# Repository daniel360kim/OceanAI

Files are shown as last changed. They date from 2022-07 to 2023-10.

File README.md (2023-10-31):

<!-- Project Logo -->
<div align="center">

<a href="https://github.com/daniel360kim/OceanAI">
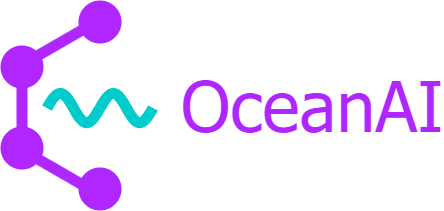
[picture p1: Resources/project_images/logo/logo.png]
    
</a>
  <h1 align="center">OceanAI</h1>
  
  <p align="center">
    A robotic and software orientated ocean development.
    <br />
    <a href="https://www.youtube.com/watch?v=8TJVxcPY-2g&t=32s&ab_channel=NMRocketry"><strong>See the video »</strong></a>
    <br />
    <br />
  </p>
</div>

<br>
  <h2>Table of Contents</h2>
  <ol>
    <li>
      <a href="#about-the-project">About The Project</a>
    </li>
    <li>
      <a href="#getting-started">Getting Started</a>
      <ul>
        <li><a href="#AUV Software">AUV Software</a></li>
        <li><a href="#Graphical User Interface">Graphical User Interface</a></li>
      </ul>
    </li>
    <li><a href="#license">License</a></li>
    <li><a href="#contact">Contact</a></li>
  </ol>

# About the Project
This project aims at creating an autonomous underwater vehicle (AUV) that utilizes cameras, sensors, a microcontroller, and GPS to categorize, identify, and map underwater trash. Detection of litter will be performed with a deep learning model - optimized to run on a microcontroller - allowing for cheap and power-efficient inference of underwater footage.

Main components of the project include:
* [AUV Control Board](https://github.com/daniel360kim/OceanAI/tree/master/PCBs)
* [AUV Software](https://github.com/daniel360kim/OceanAI/tree/master/software/sub_driver)
* [AUV CAD Model](https://github.com/daniel360kim/OceanAI/tree/master/CAD)
* [Deep Learning Model](https://github.com/daniel360kim/OceanAI/tree/master/software/detection_model)

# Getting Started
## AUV Software
[VSCode](https://code.visualstudio.com/) and
[PlatformIO](https://platformio.org/) are used to build and upload the software to the AUV.
1. Install VSCode and the PlatformIO extension.
2. Clone the repository.
```sh
git clone https://github.com/daniel360kim/OceanAI.git
```
3. Go to PlatformIO home and go to the 'Projects' tab.
4. Click 'Add Existing Project' and select the `software/sub_driver` folder.
5. Make sure you have the Teensy 4.1 core installed.
6. Connect the AUV through USB and click the 'Upload' button.
<br></br>

## Graphical User Interface

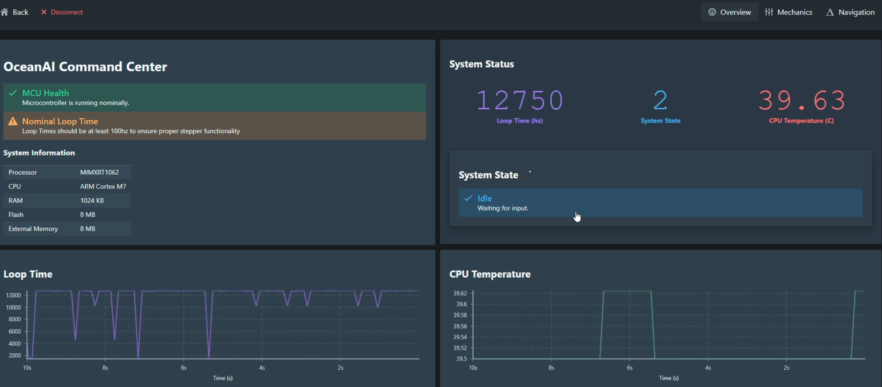
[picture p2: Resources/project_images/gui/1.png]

<br></br>
The GUI is built using [ElectricUI](https://electricui.com/). ElectricUI requires:
* [Node.js](https://nodejs.org/en/)
* [Yarn](https://yarnpkg.com/)

1. Install Node.js, [available from their website](https://nodejs.org/en/).
2. Install Yarn.
```sh
npm install -g yarn
```
3. Install ElectricUI, [available here](https://registry.eui.io/arc/latest/arc_latest_windows_amd64.msi)
4. Check everything installed and can be found in your PATH
```sh
arc info
```
5. Clone the repository if you haven't already.
```sh
git clone https://github.com/daniel360kim/OceanAI.git
```
6. Open the GUI project with ElectricUI. `software/auv_gui`
7. Run the GUI.
```sh
arc start
```

# License
Distributed under the MIT License. See `LICENSE` for more information.

# Contact
* Daniel Kim - nmrs.thrust@gmail.com - [YouTube](https://www.youtube.com/channel/UC0VazqJrUQiJGd_Tedn47zA) - Instagram: @us_rockets
* Project Link: https://github.com/daniel360kim/OceanAI

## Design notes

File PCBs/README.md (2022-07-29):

# PCBs
## Contains all the files for the printed circuit boards.
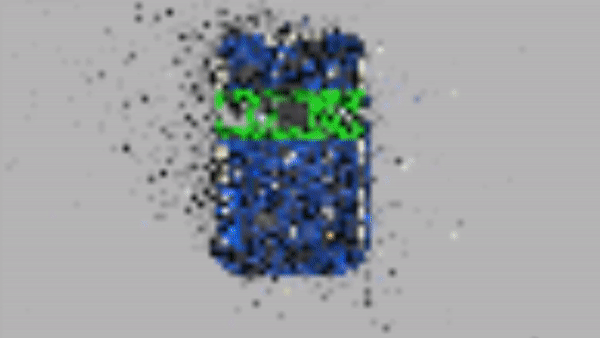
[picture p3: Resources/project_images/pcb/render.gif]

### main_board
* The PCB on the submarine that controls the submarine.
* This is the main board that controls navigation, outputs, loggins etc.

### transmitter_board
* This is an optional module that is floating in the water.
* It is connnected through a cable to the main board.
* It is above water so it can access GPS, RF, and other radio frequencies.

### sensor_board
* This board is at the front of the submarine. 
* It reads the underwater sensors and sends the data to the main board through I2C.
* It is not self powered - must have a clean 3.3V power supply.
* Programmed through SWD.

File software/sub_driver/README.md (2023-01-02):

# Sub Driver Software

Software to control the submarine driver board.

## Build
The project's directories are built with PlatformIO. To build the project, open the project in PlatformIO and click the build button.

## Dependencies Modifications
Dependencies can be modified by going to the .pio/libdeps directory within the project. 

* Must delete 
    ```cpp
    #define swap 
    ```

From Arducam dependencies to resolve conflicts with the standard library.
* Must delete utility folder from Buzzer library and remove the include from the source header file.
* Remove:
```cpp
# include "utility/pitches.h"
```
From Buzzer.h

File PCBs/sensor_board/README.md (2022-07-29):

# Transmitter Board
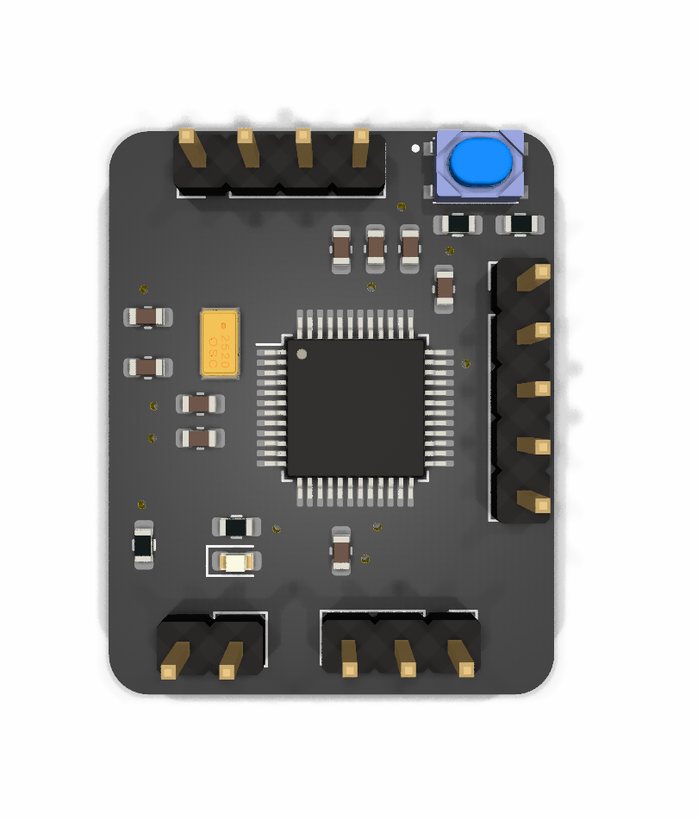
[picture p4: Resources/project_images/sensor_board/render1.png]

## This directory contains the PCB designs for the sensor board.
### The front of the submarine contains several sensors underwater: a pressure transducer and a thermistor. The pressure transducer is used to measure the pressure of the water. The thermistor is used to measure the temperature of the water. The sensor board reads these sensors and sends the data to the main board through I2C. 
### Power:
* 3.3V (no voltage regulator onboard - must be clean 3.3V)
### Sensors:
* Analog input for external pressure transducer
* 10K Thermistor for water temperature readings
### Communication:
* Communicated to the submarine [main_board](https://github.com/daniel360kim/OceanAI/tree/master/main_board) through I2C.
* The board features SWD interface for debugging and is programmed through SWD.

## What's done?
* Schematic is finished.
* PCB layout is finished
* 3D models and fabrication outputs are generated
## What's to do?
* Ordering and fabrication

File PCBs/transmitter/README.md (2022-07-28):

# Transmitter Board
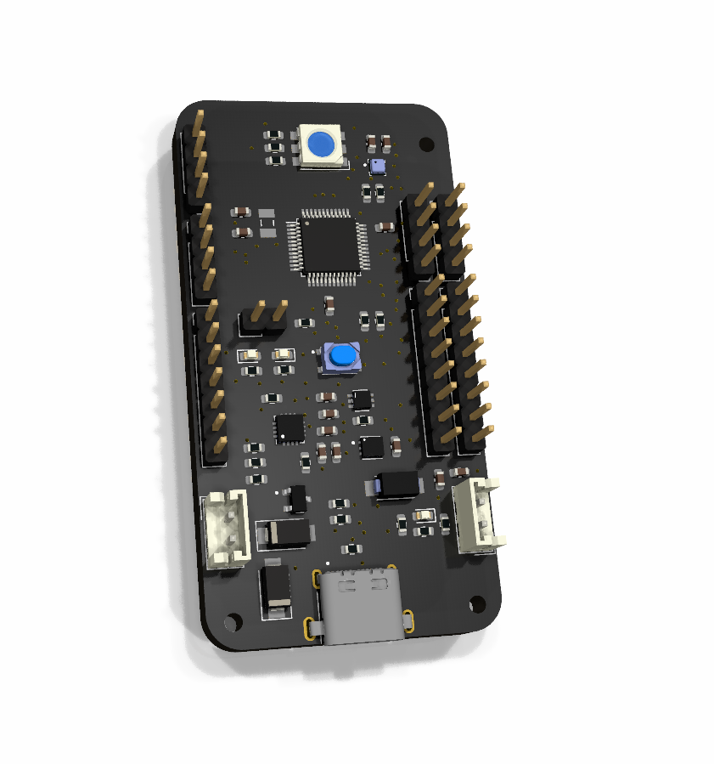
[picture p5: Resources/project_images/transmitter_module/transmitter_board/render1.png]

## This directory contains the PCB designs for the transmitter board.
### Since RF and GPS do not function well underwater, the submarine will feature an optional transmitter module that is floating in the water. The transmitter board is a simple, inexpensive, and easy to use module that can be used to transmit data to the submarine. Powered by the ATSAMD21G18A, the board has several features:
### Power:
* 1S LiPo battery 
* Solar power to recharge LiPo battery
### Sensors:
* BMP388 pressure sensor
* 10K Thermistor for water temperature readings
### Communication:
* Communicated to the submarine [main_board](https://github.com/daniel360kim/OceanAI/tree/master/main_board) through an ethernet cable through I2C.
* I2C optimized for long range communication using the LTC4311 chip.
* The board has 2 SPI interfaces: One for a 2.4GHz RF module and one for a LoRa radio module.
* The board has a UART interface for GPS connectivity.
* The board features SWD interface for debugging. 

## What's done?
* Schematic is finished.
* PCB layout is finished
* 3D models and fabrication outputs are generated
## What's to do?
* Ordering and fabrication

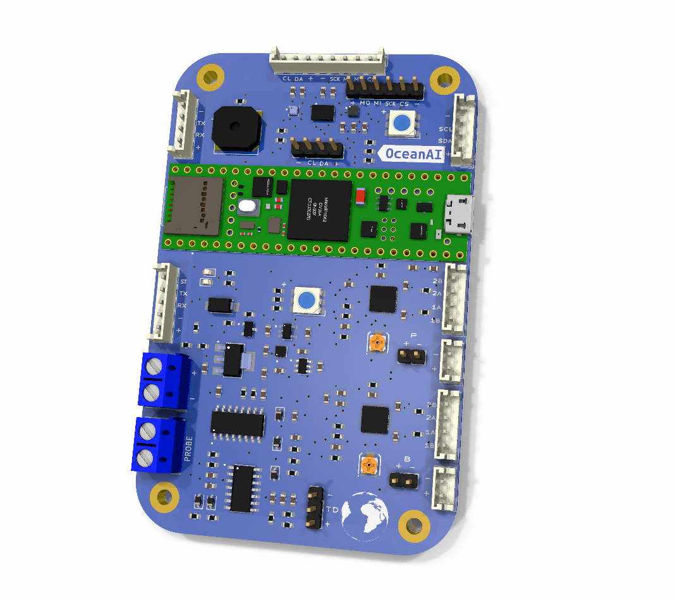
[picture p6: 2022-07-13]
PCBs/main_board/main_board_png/front_render.png

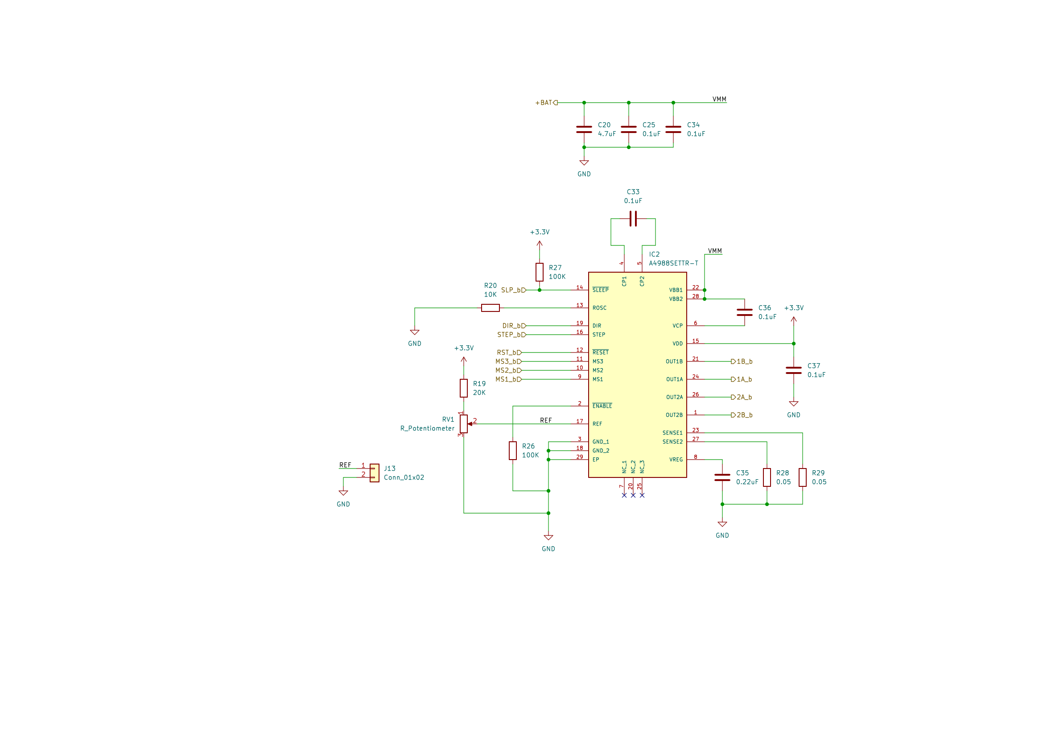
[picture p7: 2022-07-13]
PCBs/main_board/main_board_png/sch_rev2-05.png

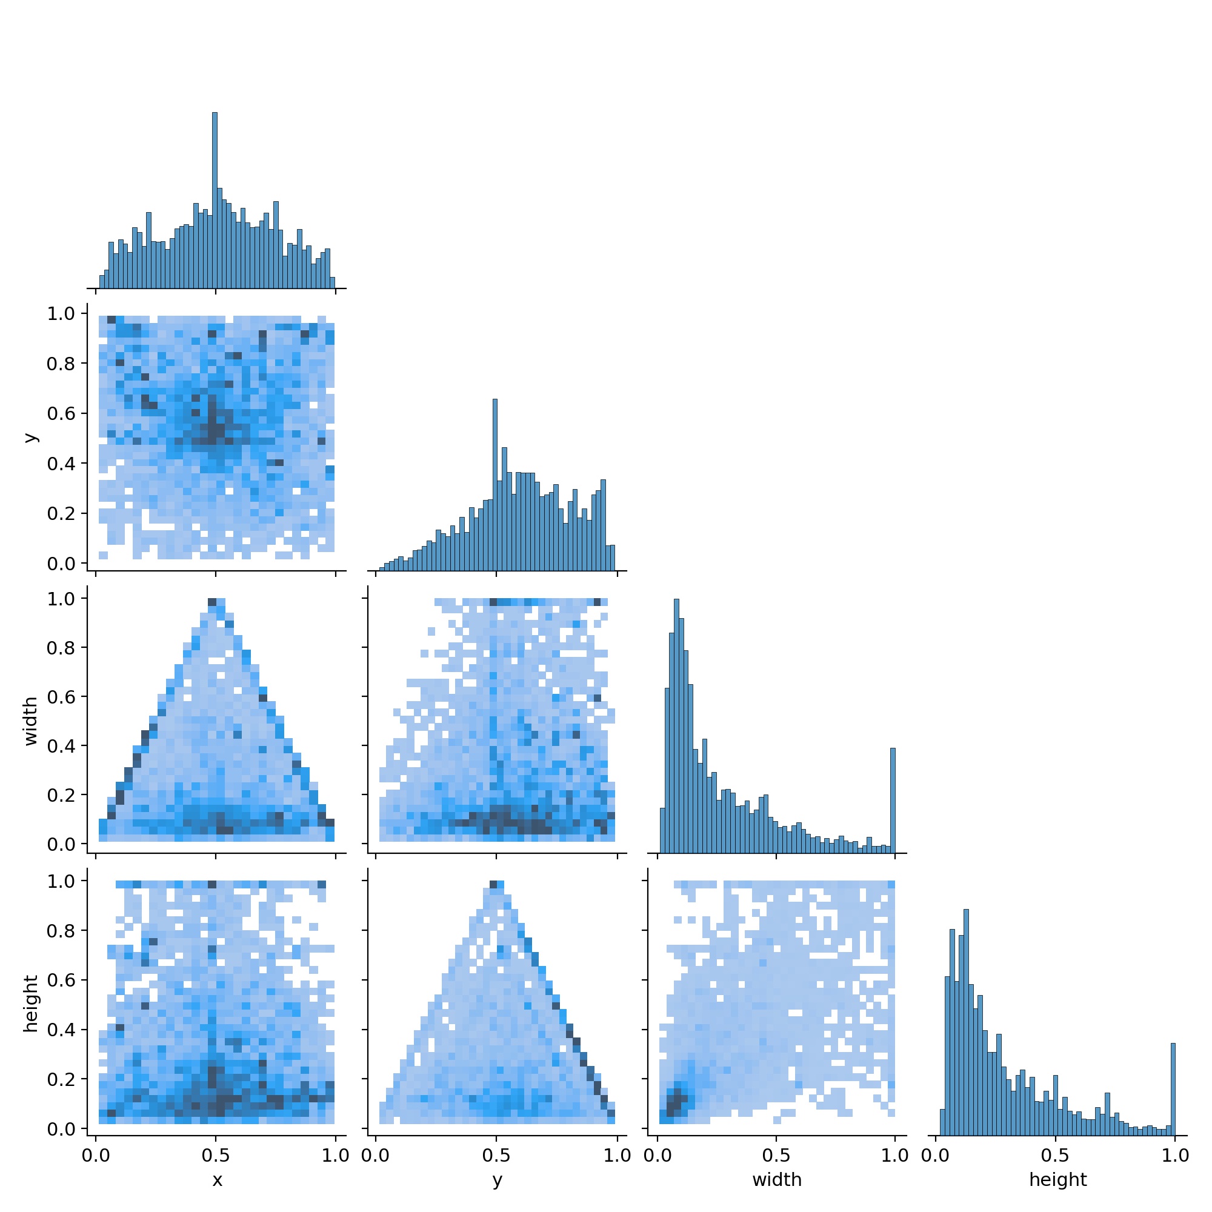
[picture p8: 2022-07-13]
Resources/project_images/object_detection/Run 1/04994b5c-de77-487a-9553-cd7c2c360d0d.jpg

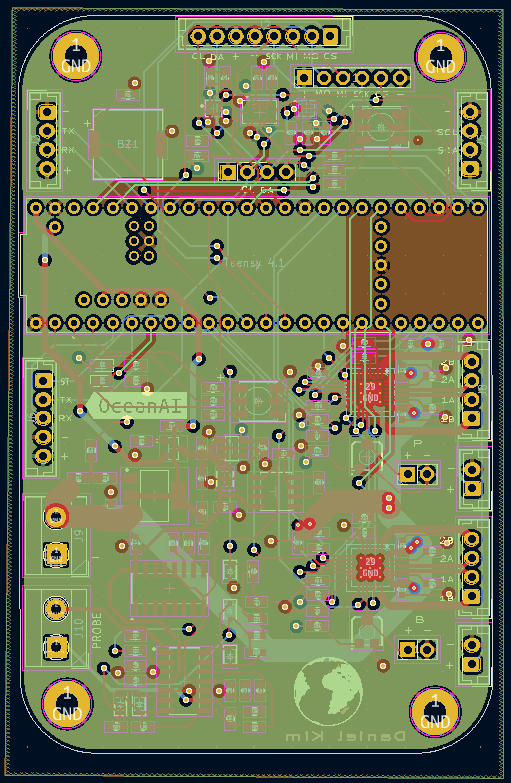
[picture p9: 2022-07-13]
PCBs/main_board/main_board_png/inner1.png

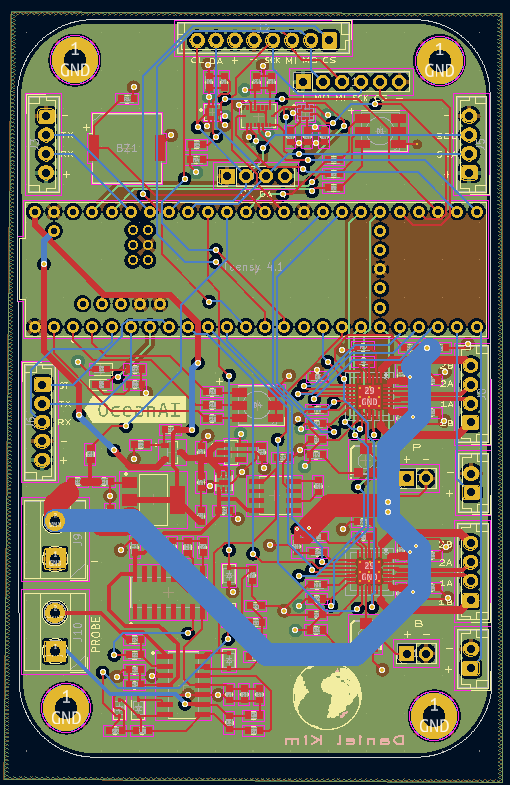
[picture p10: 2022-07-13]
PCBs/main_board/main_board_png/bottom.png

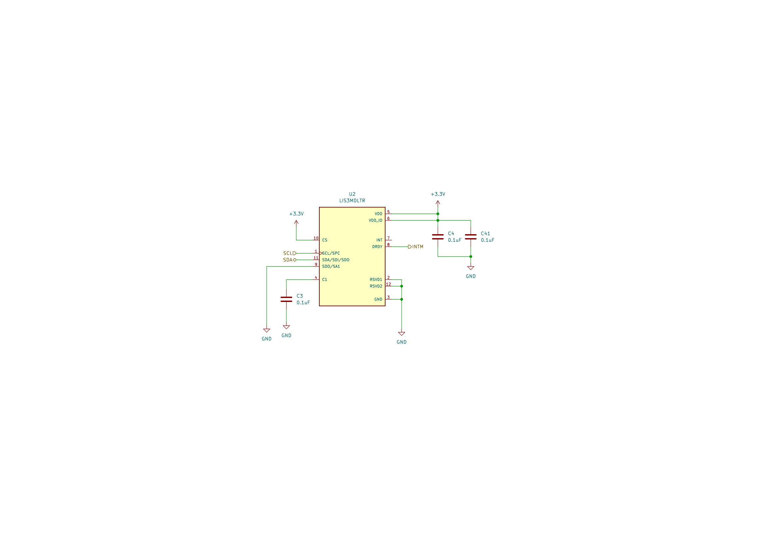
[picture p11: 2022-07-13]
PCBs/main_board/main_board_png/sch_rev2-03.png

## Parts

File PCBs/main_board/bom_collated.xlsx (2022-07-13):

Item | Item | Item | Value | LibPart | Footprint
1 | 1 | BZ1 | Buzzer | Device:Buzzer | Buzzer_Beeper:Buzzer_Murata_PKMCS0909E
2 | 21 | C1, C2, C3, C4, C5, C6, C8, C9, C14, C15, C25, C27, C28, C29, C31, C32, C33, C34, C36, C37, C41 | 0.1uF | Device:C | Capacitor_SMD:C_0603_1608Metric
3 | 1 | C7 | 1nF | Device:C | Capacitor_SMD:C_0603_1608Metric
4 | 7 | C10, C13, C17, C19, C21, C22, C24 | 1uF | Device:C | Capacitor_SMD:C_0603_1608Metric
5 | 5 | C11, C12, C20, C23, C26 | 4.7uF | Device:C | Capacitor_SMD:C_0603_1608Metric
6 | 2 | C16, C18 | 10uF | Device:C | Capacitor_SMD:C_0603_1608Metric
7 | 2 | C30, C35 | 0.22uF | Device:C | Capacitor_SMD:C_0603_1608Metric
8 | 5 | D1, D2, D3, D4, D5 | 1N4148WS | Diode:1N4148WS | Diode_SMD:D_SOD-323
9 | 2 | D6, D7 | LED_RGB | Device:LED_RGB | LED_SMD:LED_RGB_5050-6
10 | 2 | D8, D9 | LED | Device:LED | LED_SMD:LED_0603_1608Metric
11 | 4 | H1, H2, H3, H4 | MountingHole_Pad | Mechanical:MountingHole_Pad | MountingHole:MountingHole_3mm_Pad
12 | 2 | IC1, IC2 | A4988SETTR-T | A4988SETTR-T:A4988SETTR-T | A4988SETTR-T:QFN50P500X500X100-29N
13 | 1 | J1 | MS5803 | Connector_Generic:Conn_01x04 | Connector_JST:JST_EH_B4B-EH-A_1x04_P2.50mm_Vertical
14 | 1 | J2 | I2C | Connector_Generic:Conn_01x04 | Connector_PinHeader_2.54mm:PinHeader_1x04_P2.54mm_Vertical
15 | 1 | J3 | PROBE | Connector_Generic:Conn_01x02 | TerminalBlock_MetzConnect:TerminalBlock_MetzConnect_Type101_RT01602HBWC_1x02_P5.08mm_Horizontal
16 | 1 | J4 | Batt | Connector_Generic:Conn_01x02 | TerminalBlock_MetzConnect:TerminalBlock_MetzConnect_Type101_RT01602HBWC_1x02_P5.08mm_Horizontal
17 | 1 | J5 | OV5642 | Connector_Generic:Conn_01x08 | Connector_JST:JST_EH_B8B-EH-A_1x08_P2.50mm_Vertical
18 | 1 | J6 | JST_B | Connector_Generic:Conn_01x04 | Connector_JST:JST_EH_B4B-EH-A_1x04_P2.50mm_Vertical
19 | 1 | J7 | JST_P | Connector_Generic:Conn_01x04 | Connector_JST:JST_EH_B4B-EH-A_1x04_P2.50mm_Vertical
20 | 1 | J8 | I2C | Connector_Generic:Conn_01x06 | Connector_PinHeader_2.54mm:PinHeader_1x06_P2.54mm_Vertical
21 | 1 | J9 | HC-12 | Connector_Generic:Conn_01x05 | Connector_JST:JST_EH_B5B-EH-A_1x05_P2.50mm_Vertical
22 | 1 | J10 | NEO-6M | Connector_Generic:Conn_01x04 | Connector_JST:JST_EH_B4B-EH-A_1x04_P2.50mm_Vertical
23 | 1 | J11 | Limit_b | Connector_Generic:Conn_01x02 | Connector_JST:JST_EH_B2B-EH-A_1x02_P2.50mm_Vertical
24 | 1 | J12 | Limit_p | Connector_Generic:Conn_01x02 | Connector_JST:JST_EH_B2B-EH-A_1x02_P2.50mm_Vertical
25 | 2 | J13, J14 | Conn_01x02 | Connector_Generic:Conn_01x02 | Connector_PinHeader_2.54mm:PinHeader_1x02_P2.54mm_Vertical
26 | 1 | Q1 | DMP3098L-7 | DMP3098L-7:DMP3098L-7 | DMP3098L-7:SOT91P240X110-3N
27 | 1 | R1 | 1M | Device:R | Resistor_SMD:R_0603_1608Metric
28 | 3 | R2, R3, R39 | 4.7K | Device:R | Resistor_SMD:R_0603_1608Metric
29 | 1 | R4 | 5.6K | Device:R | Resistor_SMD:R_0603_1608Metric
30 | 1 | R5 | 6.8K | Device:R | Resistor_SMD:R_0603_1608Metric
31 | 6 | R6, R8, R22, R23, R26, R27 | 100K | Device:R | Resistor_SMD:R_0603_1608Metric
32 | 10 | R7, R9, R10, R11, R12, R13, R14, R15, R20, R21 | 10K | Device:R | Resistor_SMD:R_0603_1608Metric
33 | 1 | R16 | 2.5 | Device:R | Resistor_SMD:R_0603_1608Metric
34 | 4 | R17, R18, R31, R41 | 1K | Device:R | Resistor_SMD:R_0603_1608Metric
35 | 2 | R19, R30 | 20K | Device:R | Resistor_SMD:R_0603_1608Metric
36 | 4 | R24, R25, R28, R29 | 0.05 | Device:R | Resistor_SMD:R_0603_1608Metric
37 | 4 | R33, R35, R36, R38 | R | Device:R | Resistor_SMD:R_0603_1608Metric
38 | 2 | R34, R37 |  | Device:R | Resistor_SMD:R_0603_1608Metric
39 | 1 | R40 | 470 | Device:R | Resistor_SMD:R_0603_1608Metric
40 | 2 | RV1, RV2 | R_Potentiometer | Device:R_Potentiometer | 35WR10KLFTR:TRIM_35WR10KLFTR
41 | 1 | U1 | BMI088 | TBC_Sensors:BMI088 | BMI088:PQFN50P450X300X100-16N
42 | 1 | U2 | LIS3MDLTR | LIS3MDLTR:LIS3MDLTR | LIS3MDLTR:XDCR_LIS3MDLTR
43 | 1 | U3 | BMP388 | TBC_Sensors:BMP388 | BMP388:PQFN50P200X200X80-10N
44 | 1 | U4 | DEV-16771 | DEV-16771:DEV-16771 | DEV-16771:MODULE_DEV-16771
45 | 1 | U5 | LM324A | :LM324A_1 | LM324:SOIC127P600X175-14N
46 | 1 | U6 | CD4060BM | CD4060BM:CD4060BM | CD4060BM:SOIC127P600X175-16N
47 | 1 | U7 | ICL7662CBA-T | ICL7662CBA-T:ICL7662CBA-T | ICL7662CBA-T:SOIC127P600X175-8N
48 | 1 | U8 | AP2112K-3.3 | Regulator_Linear:AP2112K-3.3 | AP2112K-3:SOT95P285X140-5N
49 | 1 | U9 | ADP122 | ADP122:ADP122ACPZ-3.3-R7 | ADP122:SON65P200X200X65-7N
50 | 1 | U10 | LDL1117S50R | Regulator_Linear:LDL1117S50R | SOT230P700X180-4N:SOT230P700X180-4N

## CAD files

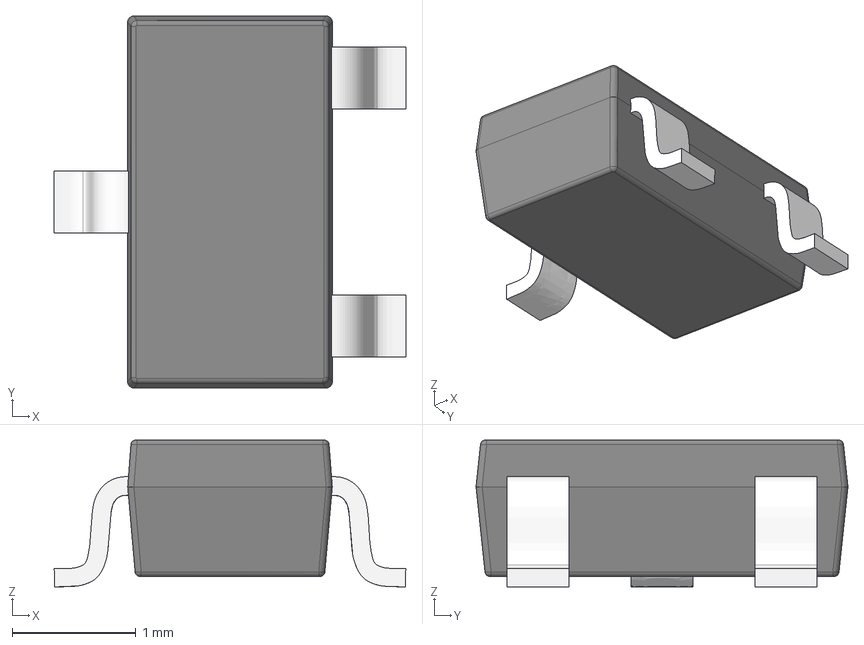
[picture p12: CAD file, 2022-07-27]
PCBs/transmitter/Dependencies/SOT23-3.stp
2.84 x 3.00 x 1.18 mm

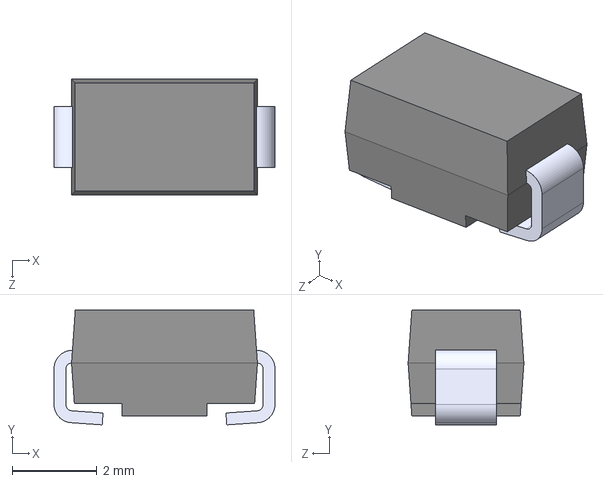
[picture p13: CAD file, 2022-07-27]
PCBs/transmitter/Dependencies/SS12.STEP
5.20 x 2.70 x 2.73 mm

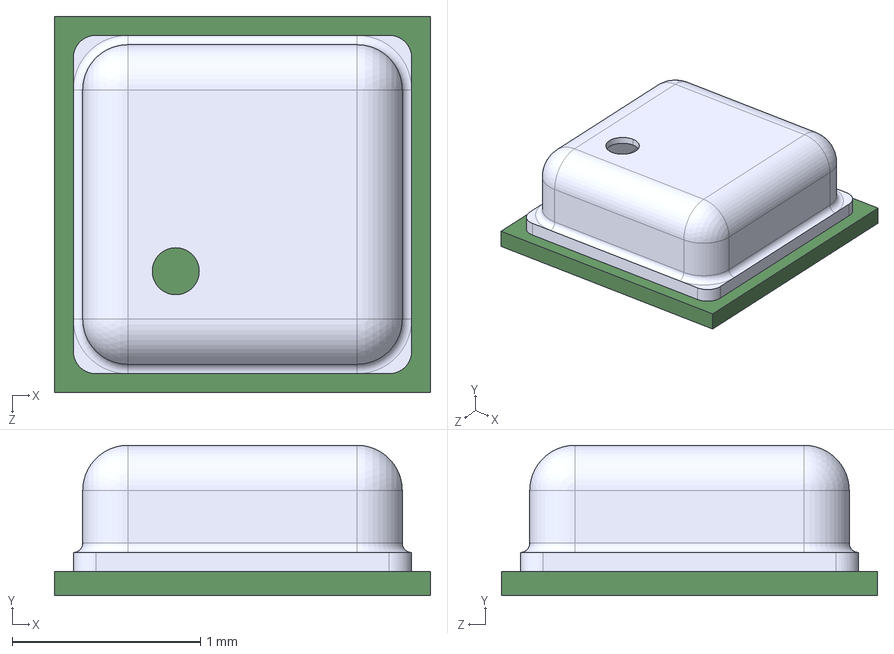
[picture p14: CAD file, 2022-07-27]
PCBs/transmitter/Dependencies/BMP388.STEP
2.00 x 0.8 x 2.00 mm

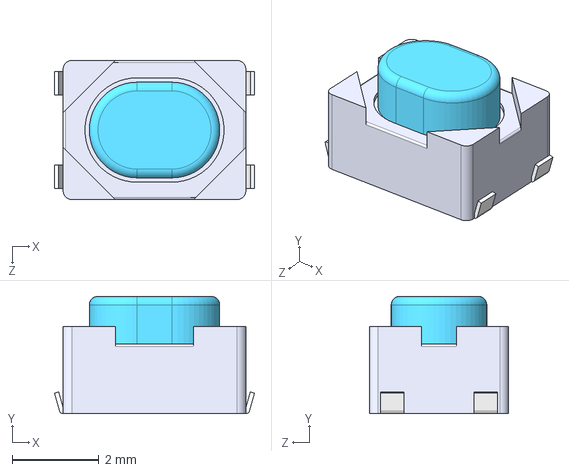
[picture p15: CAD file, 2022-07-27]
PCBs/transmitter/Dependencies/PTS810SJK250SMTRLFS.step
4.60 x 2.70 x 3.20 mm

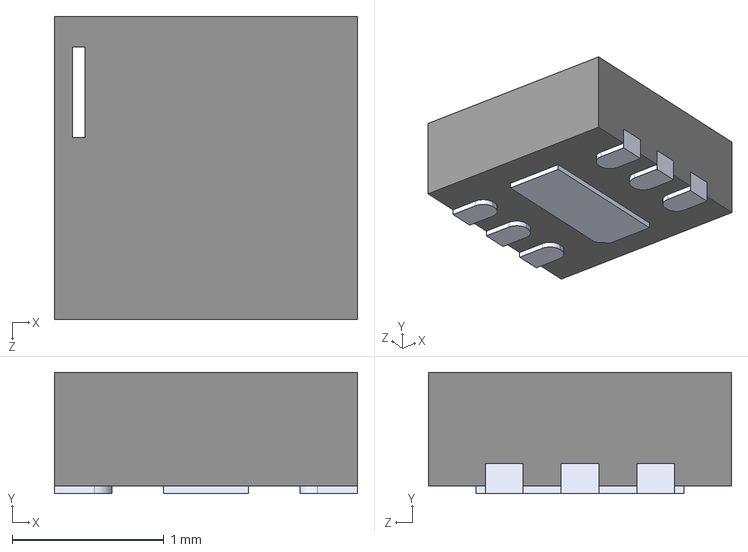
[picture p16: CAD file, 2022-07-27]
PCBs/transmitter/Dependencies/LTC4311IDCPBF.step
2.00 x 0.8 x 2.00 mm

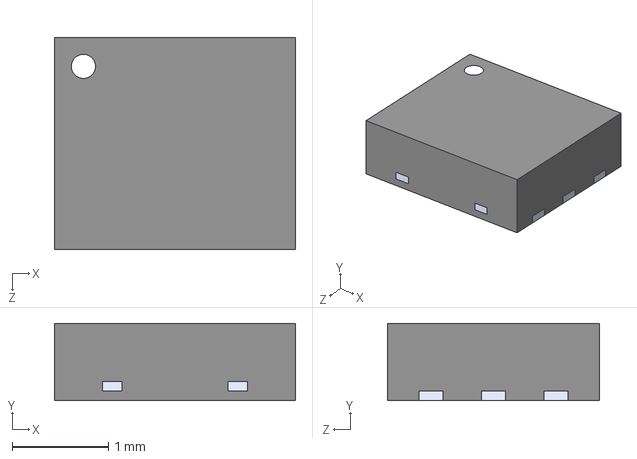
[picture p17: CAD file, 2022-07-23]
PCBs/transmitter/Dependencies/LP5900SD-3.3_NOPB.step
2.50 x 0.8 x 2.20 mm

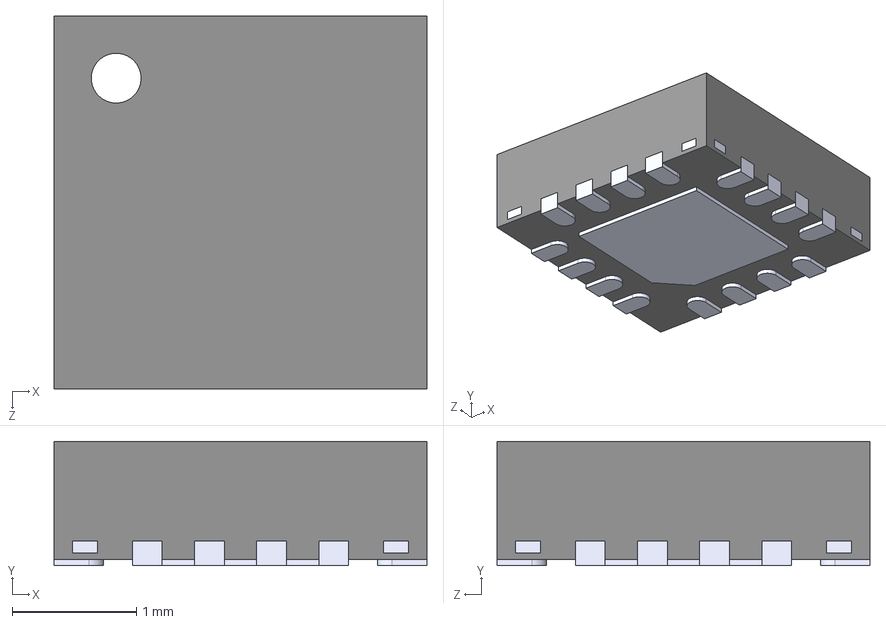
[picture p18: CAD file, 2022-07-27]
PCBs/transmitter/Dependencies/BQ24074RGTRG4.STEP
3.00 x 1.00 x 3.00 mm

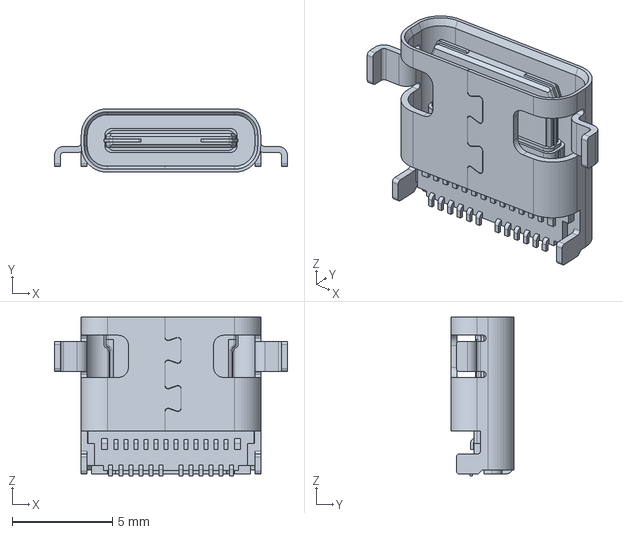
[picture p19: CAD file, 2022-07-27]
PCBs/transmitter/Dependencies/1054550101.step
11.6 x 3.16 x 7.90 mm

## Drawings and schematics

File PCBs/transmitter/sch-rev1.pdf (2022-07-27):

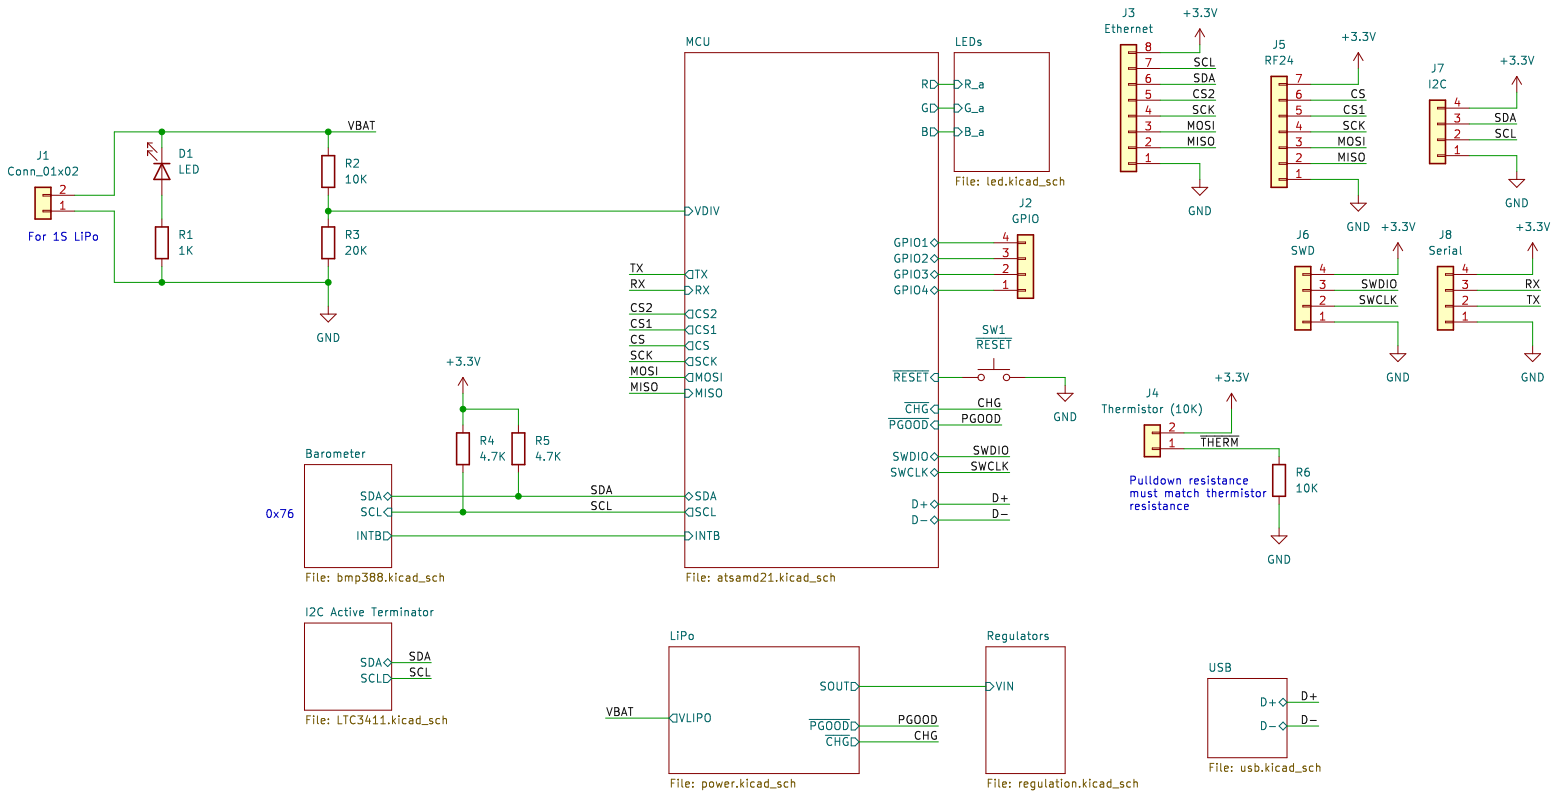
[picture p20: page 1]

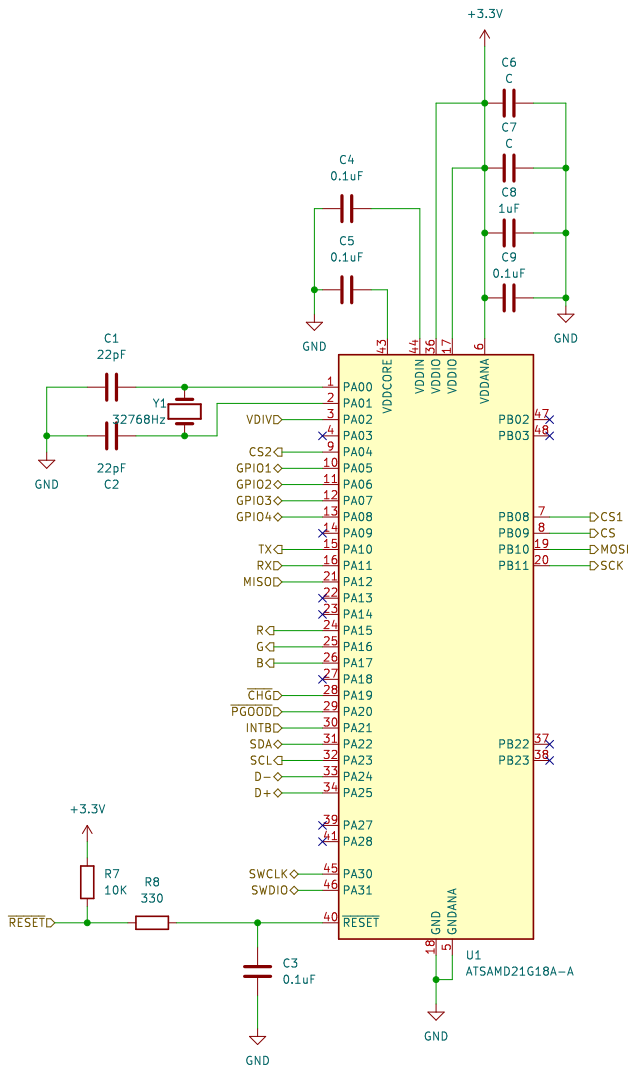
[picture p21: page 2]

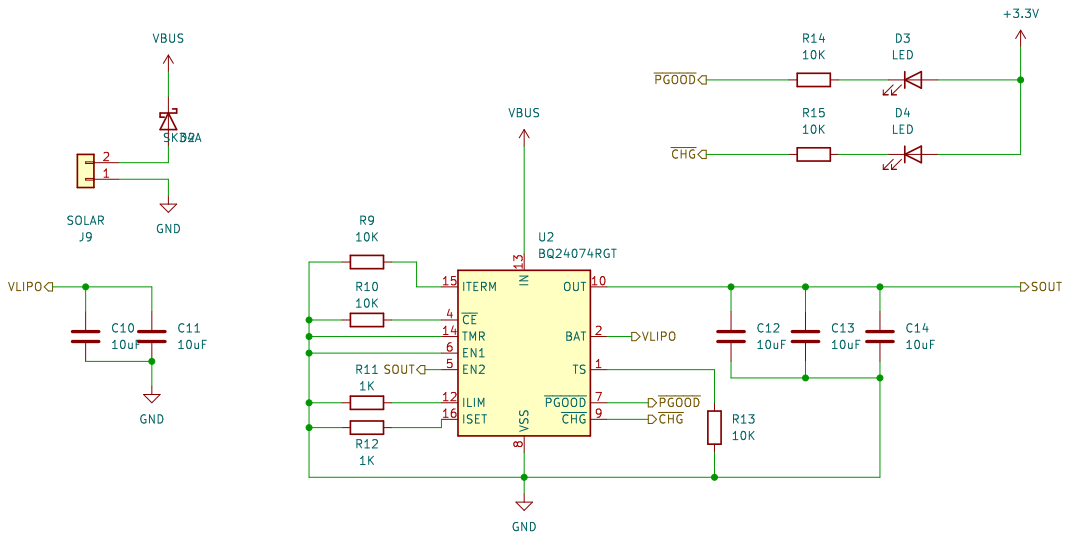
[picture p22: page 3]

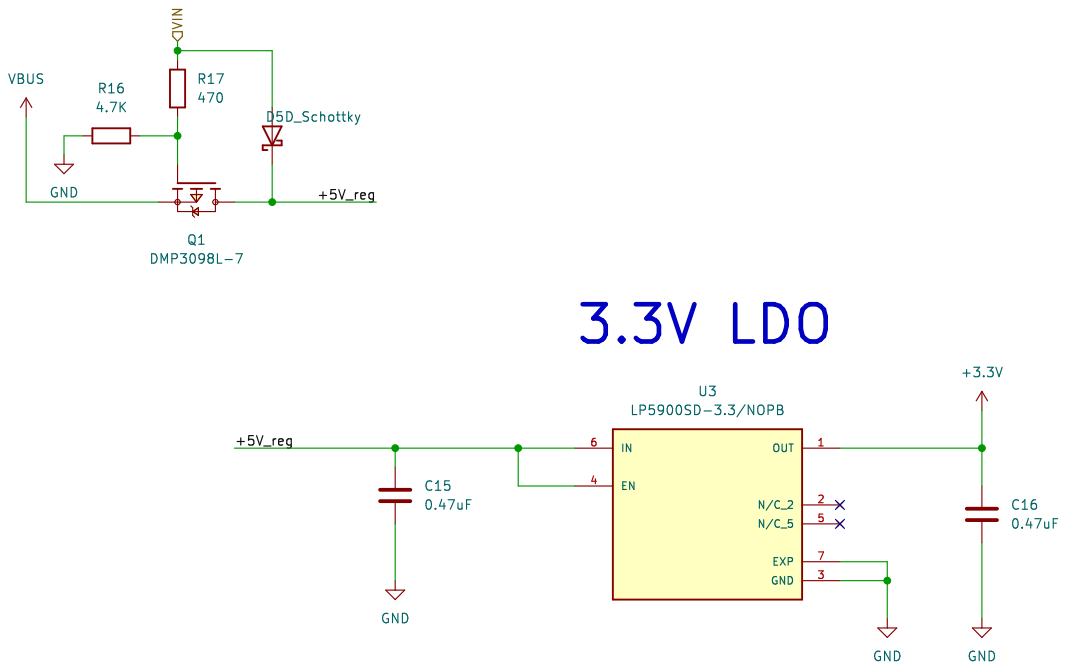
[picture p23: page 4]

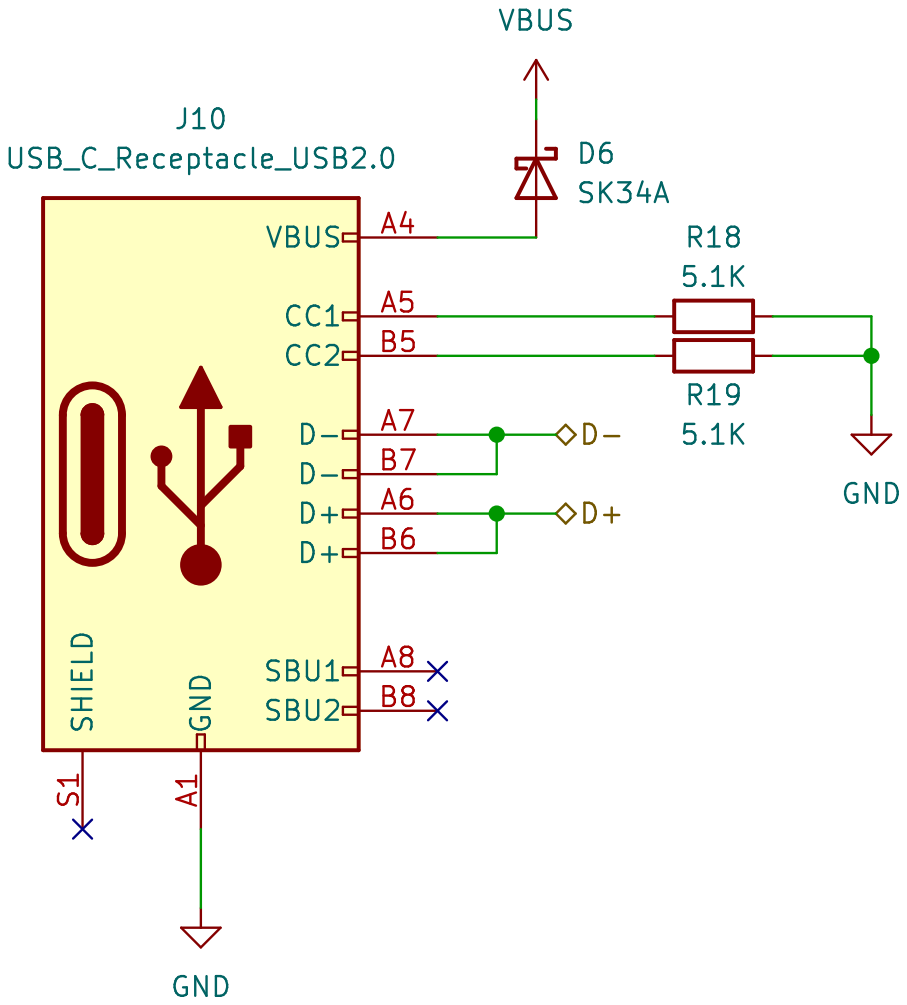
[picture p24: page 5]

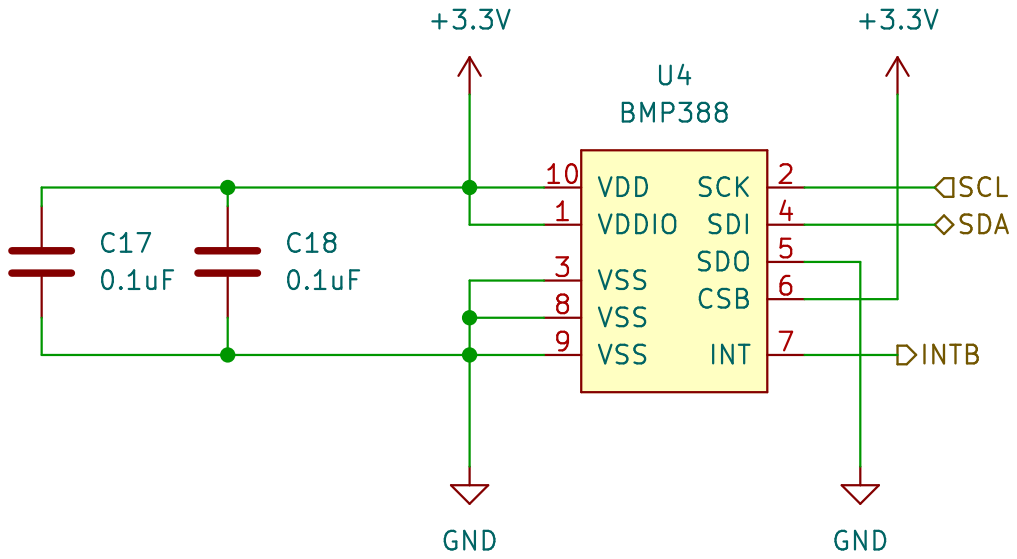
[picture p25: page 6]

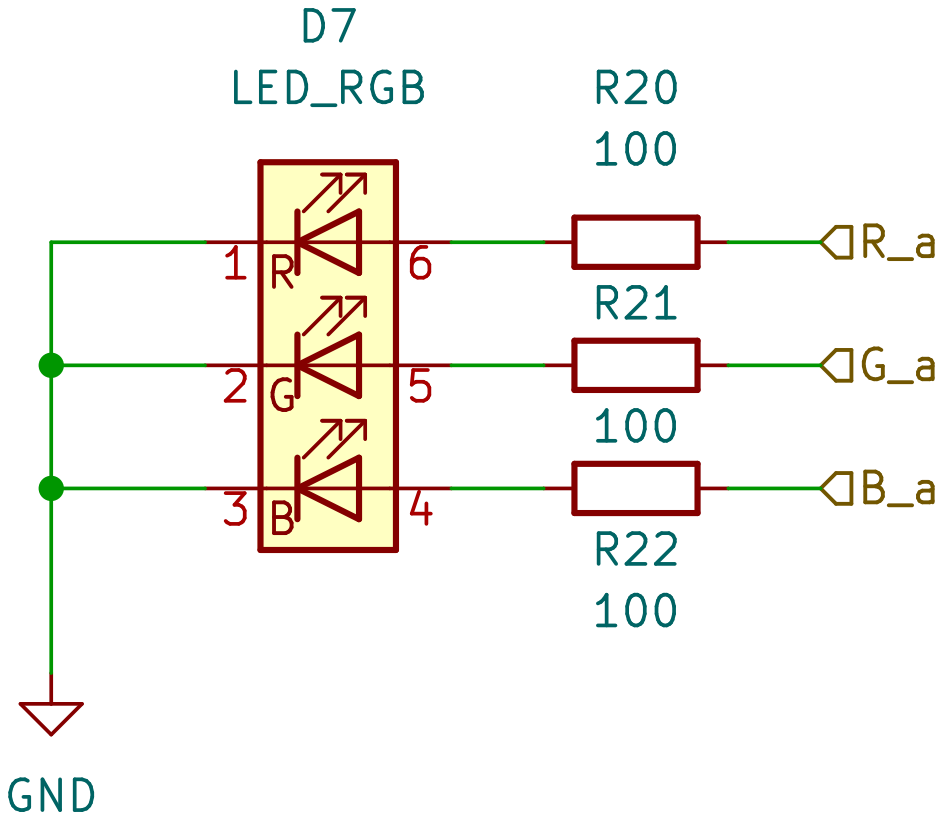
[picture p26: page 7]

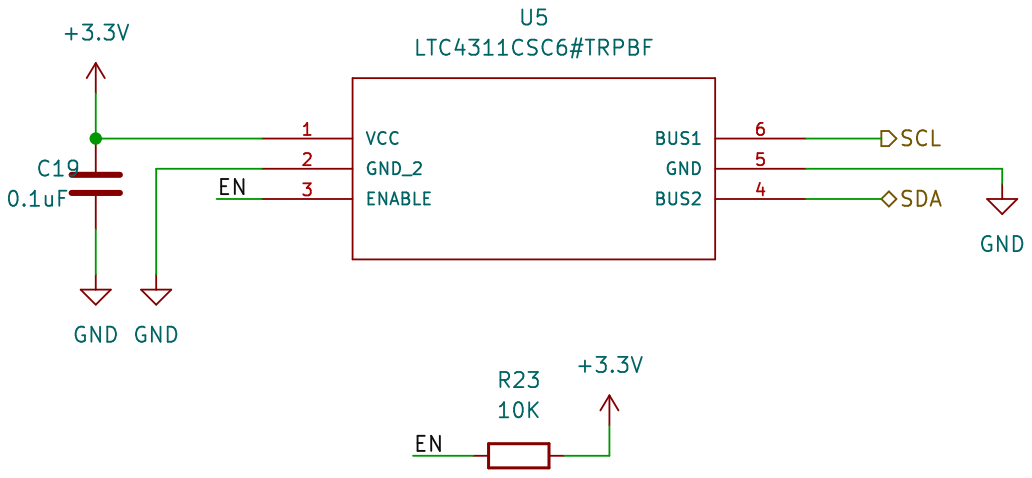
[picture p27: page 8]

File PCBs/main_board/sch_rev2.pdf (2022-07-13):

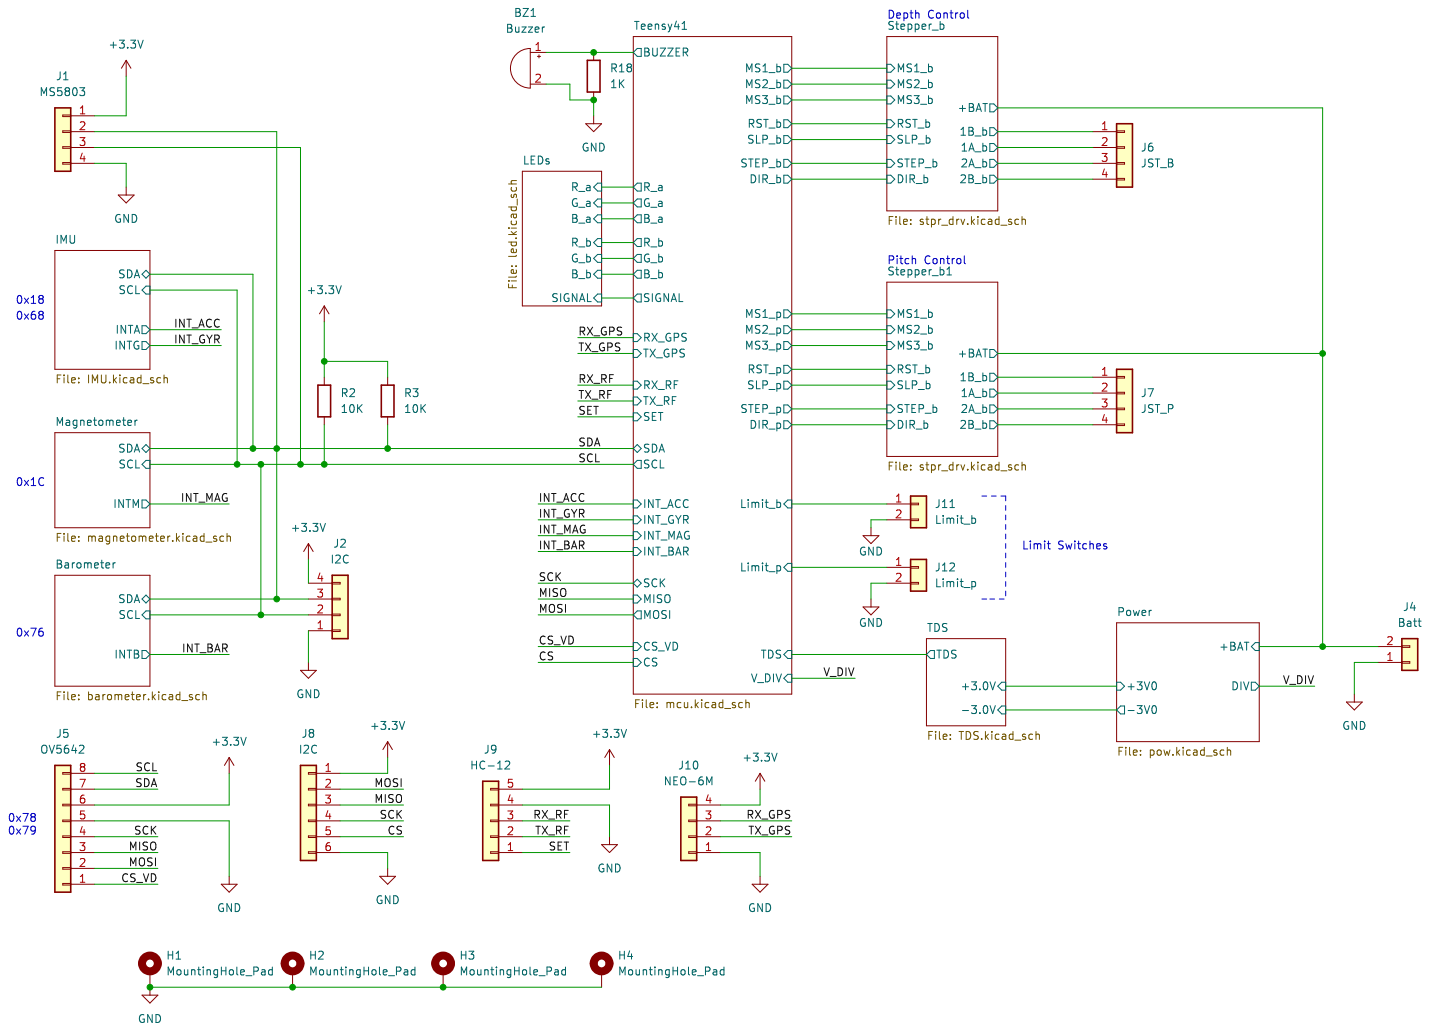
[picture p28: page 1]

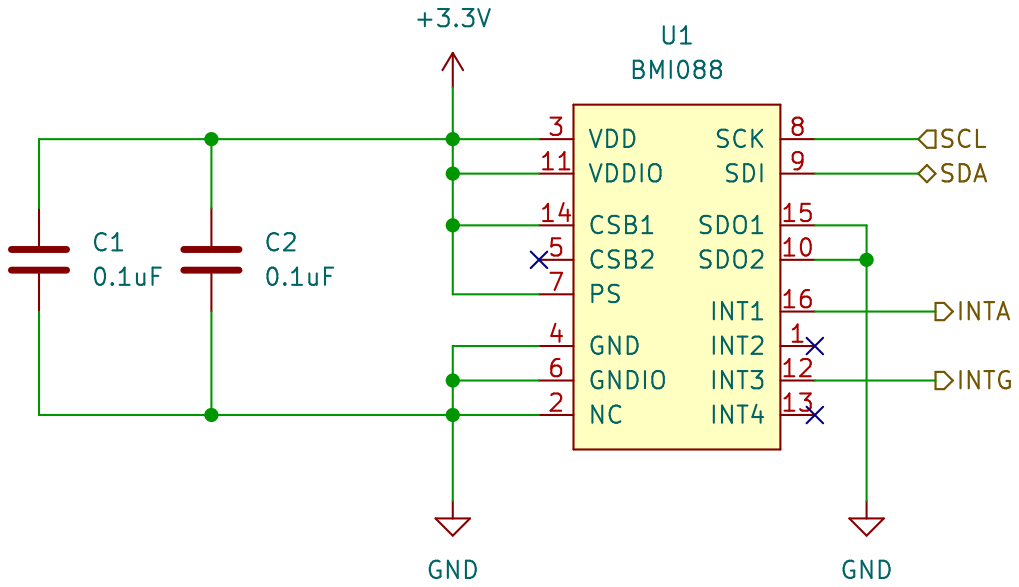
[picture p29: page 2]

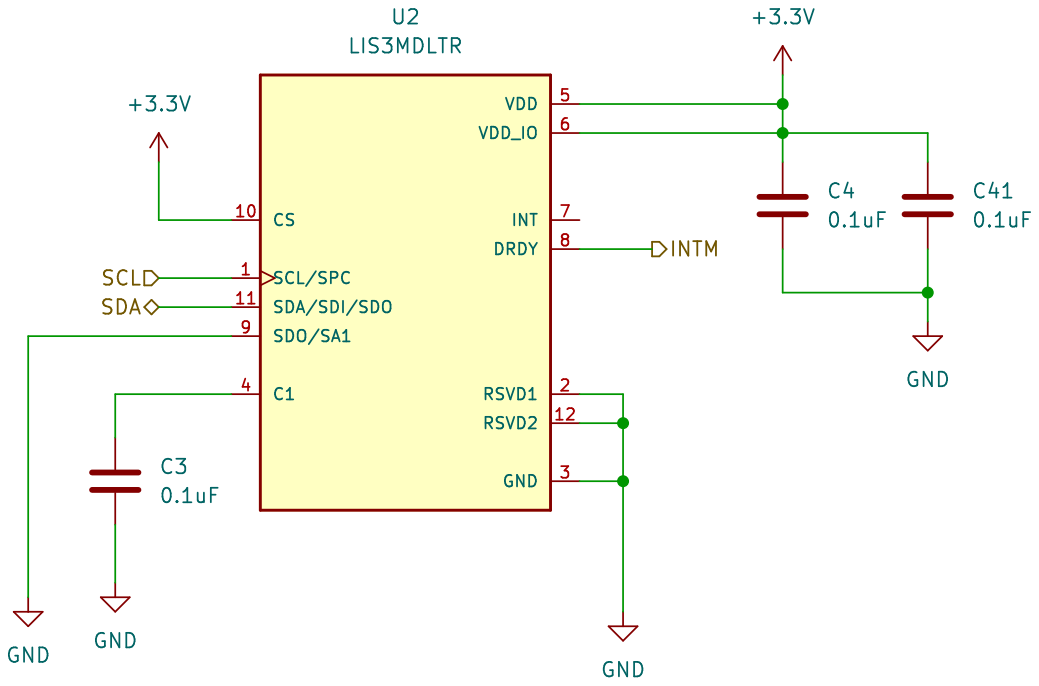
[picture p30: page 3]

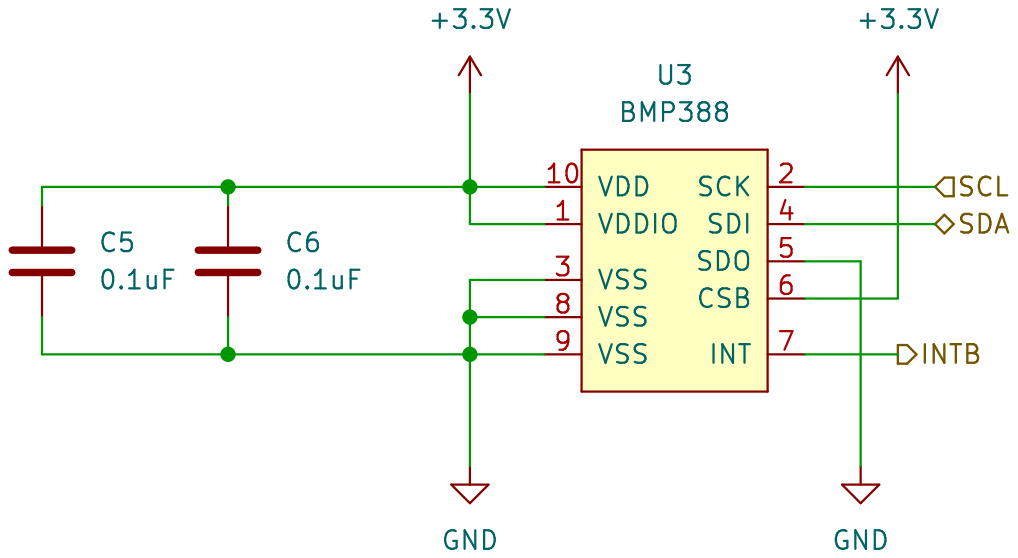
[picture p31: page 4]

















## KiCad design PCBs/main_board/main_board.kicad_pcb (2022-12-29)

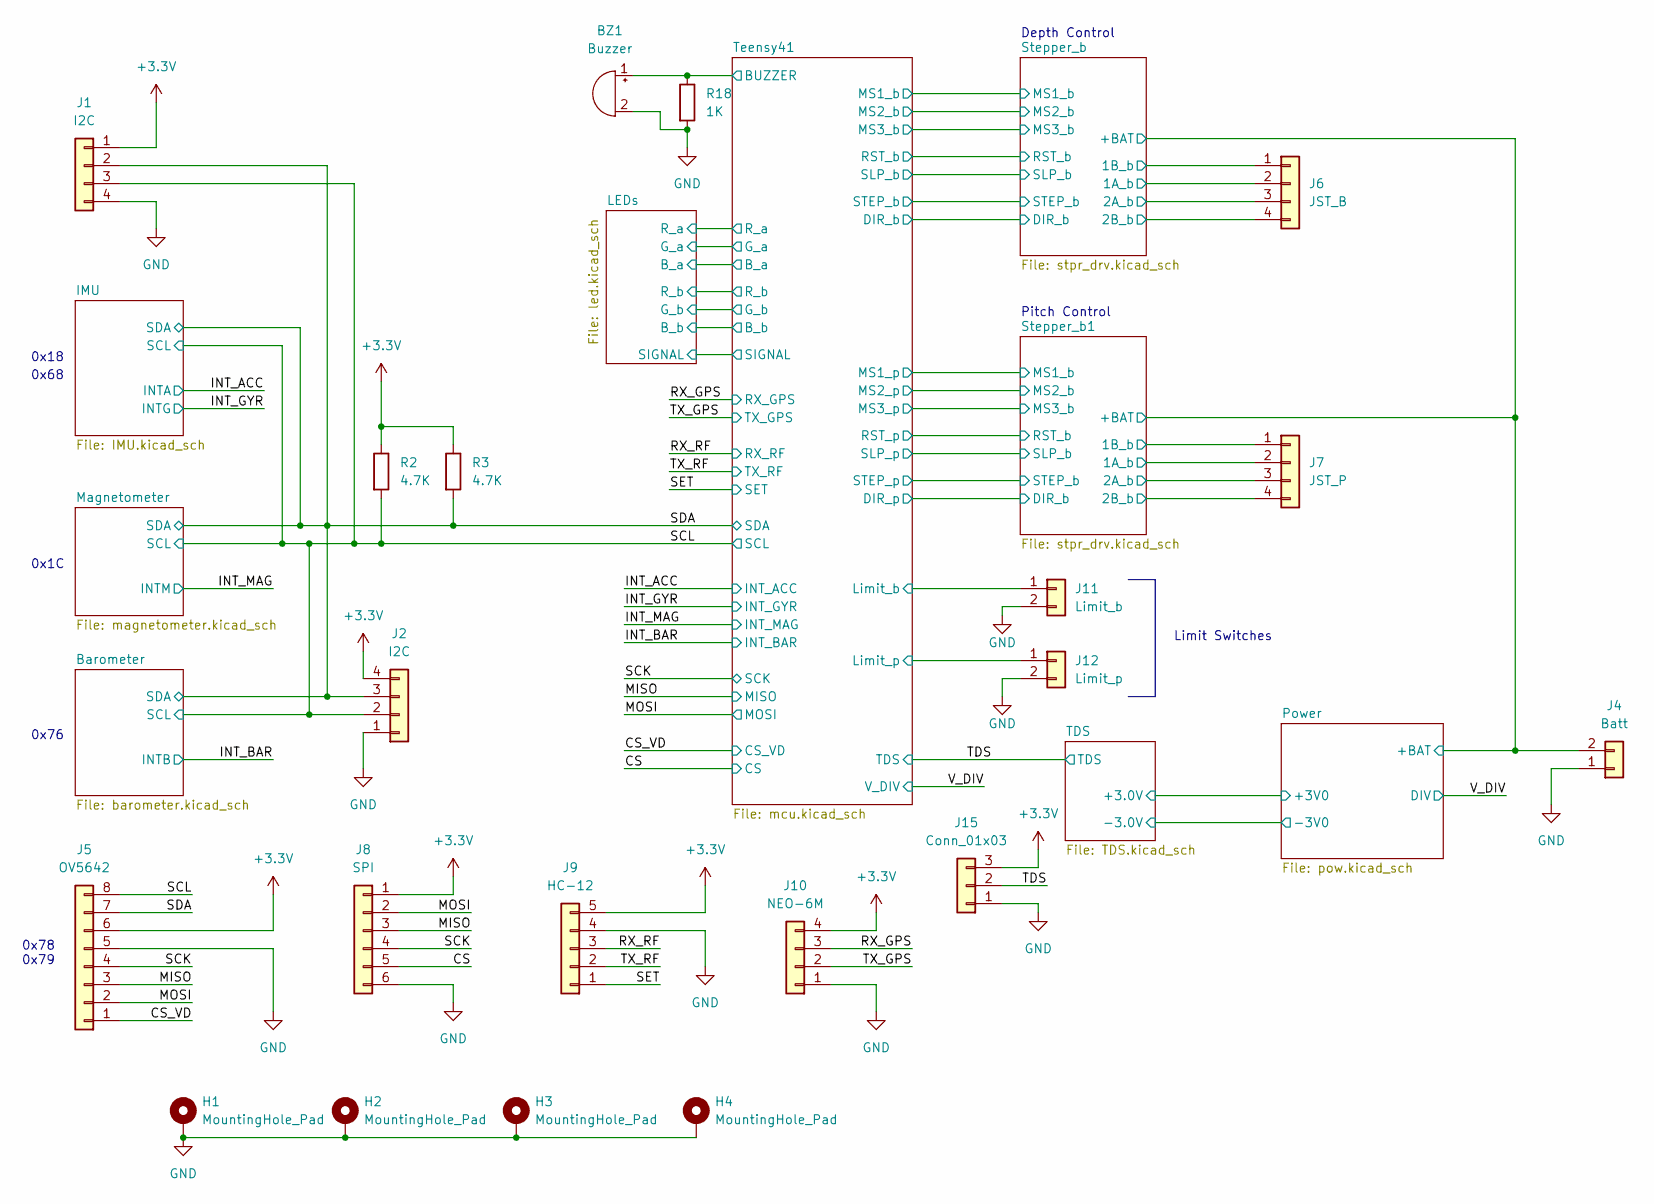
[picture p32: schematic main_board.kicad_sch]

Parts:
BZ1: Buzzer; Buzzer_Murata_PKMCS0909E
H1, H2, H3, H4: MountingHole_Pad; MountingHole_3mm_Pad
J1: I2C; JST_EH_B4B-EH-A_1x04_P2.50mm_Vertical
J2: I2C; PinHeader_1x04_P2.54mm_Vertical
J4: Batt; TerminalBlock_MetzConnect_Type101_RT01602HBWC_1x02_P5.08mm_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
J5: OV5642; JST_EH_B8B-EH-A_1x08_P2.50mm_Vertical
J6: JST_B; JST_EH_B4B-EH-A_1x04_P2.50mm_Vertical
J7: JST_P; JST_EH_B4B-EH-A_1x04_P2.50mm_Vertical
J8: SPI; PinHeader_1x06_P2.54mm_Vertical
J9: HC-12; JST_EH_B5B-EH-A_1x05_P2.50mm_Vertical
J10: NEO-6M; JST_EH_B4B-EH-A_1x04_P2.50mm_Vertical
J11: Limit_b; JST_EH_B2B-EH-A_1x02_P2.50mm_Vertical
J12: Limit_p; JST_EH_B2B-EH-A_1x02_P2.50mm_Vertical
J15: Conn_01x03; PinHeader_1x03_P2.54mm_Vertical
R2, R3: 4.7K; R_0603_1608Metric
R18: 1K; R_0603_1608Metric

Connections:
+3V3: J1.1, J2.4, J5.6, J8.1, J9.5, J10.4, J15.3, R2.1, R3.1; also elsewhere on the board
/CS: J8.5; also elsewhere on the board
/CS_VD: J5.1; also elsewhere on the board
/MISO: J5.3, J8.3; also elsewhere on the board
/MOSI: J5.2, J8.2; also elsewhere on the board
/RX_GPS: J10.3; also elsewhere on the board
/RX_RF: J9.3; also elsewhere on the board
/SCK: J5.4, J8.4; also elsewhere on the board
/SCL: J1.3, J2.2, J5.8, R2.2; also elsewhere on the board
/SDA: J1.2, J2.3, J5.7, R3.2; also elsewhere on the board
/SET: J9.1; also elsewhere on the board
/Stepper_b1/1A_b: J7.2; also elsewhere on the board
/Stepper_b1/1B_b: J7.1; also elsewhere on the board
/Stepper_b1/2A_b: J7.3; also elsewhere on the board
/Stepper_b1/2B_b: J7.4; also elsewhere on the board
/Stepper_b/1A_b: J6.2; also elsewhere on the board
/Stepper_b/1B_b: J6.1; also elsewhere on the board
/Stepper_b/2A_b: J6.3; also elsewhere on the board
/Stepper_b/2B_b: J6.4; also elsewhere on the board
/Stepper_b/VMM: J4.2; also elsewhere on the board
/TDS: J15.2; also elsewhere on the board
/TX_GPS: J10.2; also elsewhere on the board
/TX_RF: J9.2; also elsewhere on the board
/Teensy41/BUZZER: BZ1.1 (-), R18.1; also elsewhere on the board
/Teensy41/Limit_b: J11.1; also elsewhere on the board
/Teensy41/Limit_p: J12.1; also elsewhere on the board
GND: BZ1.2 (+), H1.1, H2.1, H3.1, H4.1, J1.4, J2.1, J4.1, J5.5, J8.6, J9.4, J10.1, J11.2, J12.2, J15.1, R18.2; also elsewhere on the board

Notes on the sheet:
Depth Control
0x1C
0x68
0x76
0x18
Pitch Control
Limit Switches
0x78 0x79

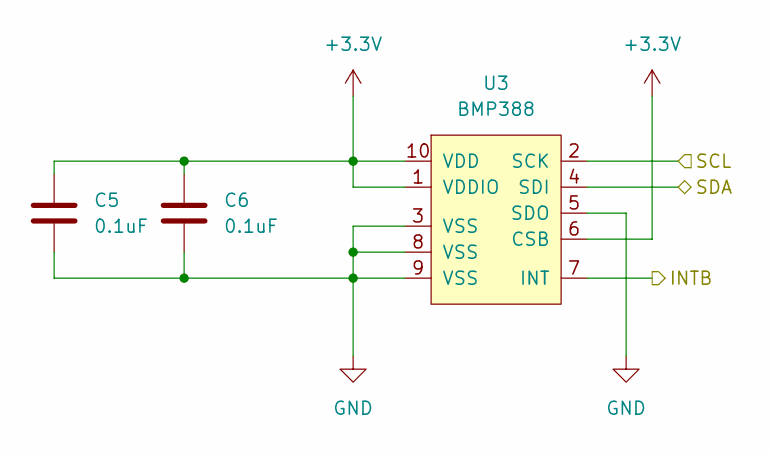
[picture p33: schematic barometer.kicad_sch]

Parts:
C5, C6: 0.1uF; C_0603_1608Metric
U3: BMP388; PQFN50P200X200X80-10N

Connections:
+3V3: C5.1, C6.1, U3.1 (VDDIO), U3.6 (CSB), U3.10 (VDD); also elsewhere on the board
/INT_BAR: U3.7 (INT); also elsewhere on the board
/SCL: U3.2 (SCK); also elsewhere on the board
/SDA: U3.4 (SDI); also elsewhere on the board
GND: C5.2, C6.2, U3.3 (VSS), U3.5 (SDO), U3.8 (VSS), U3.9 (VSS); also elsewhere on the board

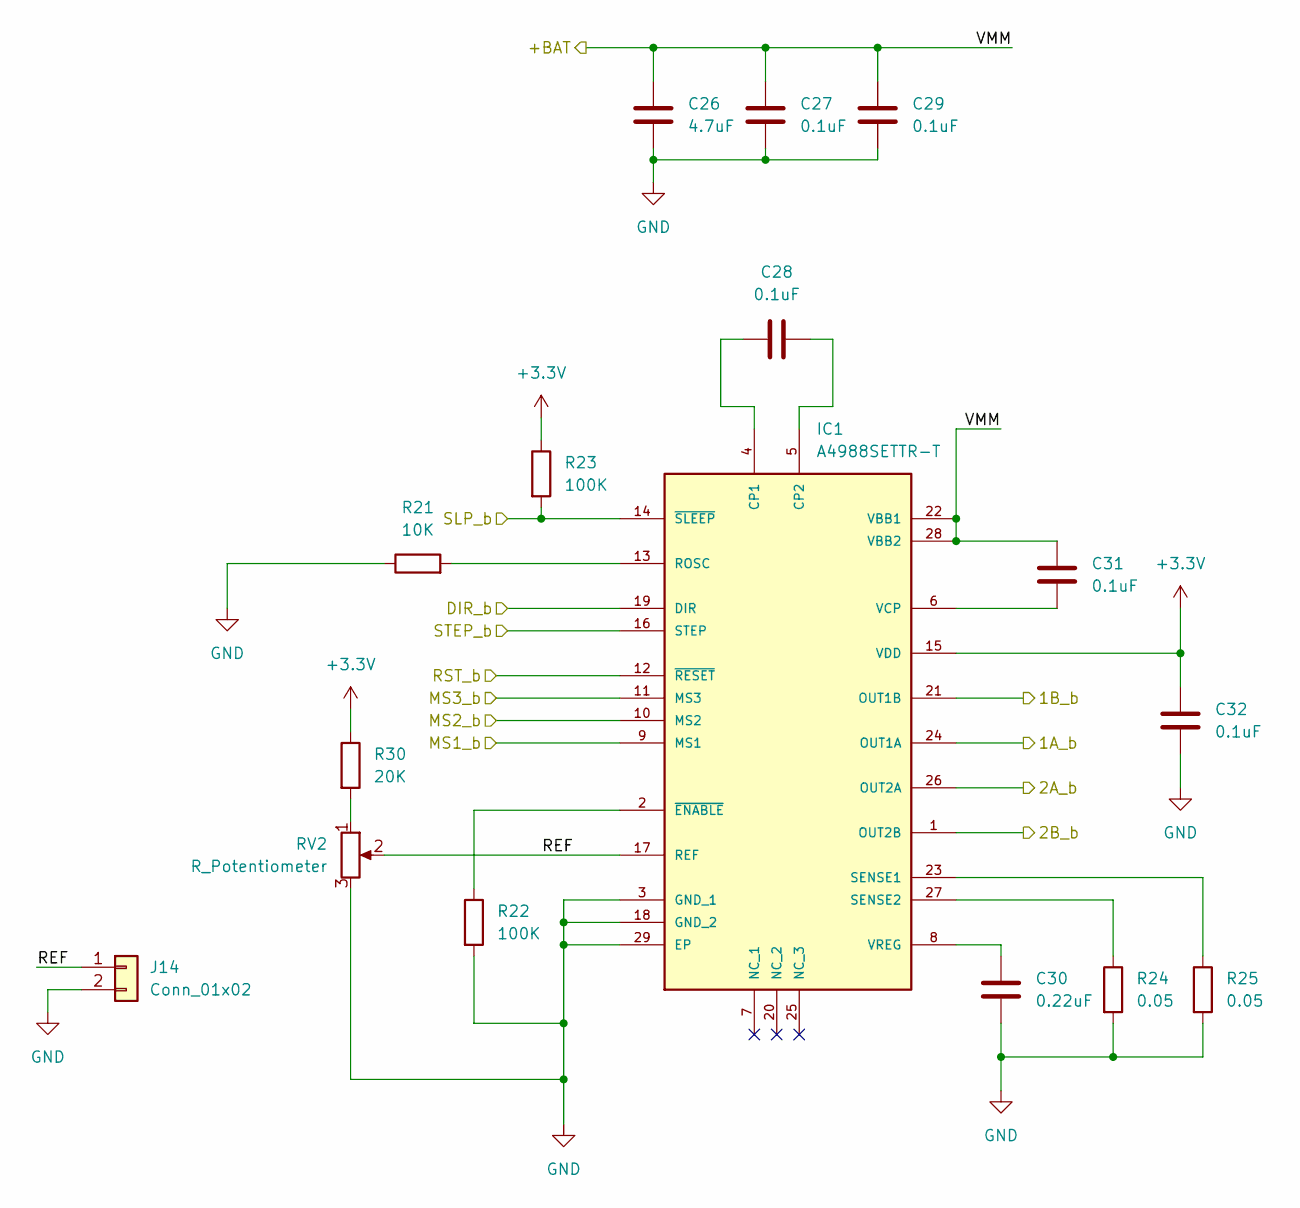
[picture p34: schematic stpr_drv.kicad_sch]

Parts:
C26: 4.7uF; C_0603_1608Metric
C27, C28, C29, C31, C32: 0.1uF; C_0603_1608Metric
C30: 0.22uF; C_0603_1608Metric
IC1: A4988SETTR-T; QFN50P500X500X100-29N; MANUFACTURER_PART_NUMBER A4988SETTR-T
J14: Conn_01x02; PinHeader_1x02_P2.54mm_Vertical
R21: 10K; R_0603_1608Metric
R22, R23: 100K; R_0603_1608Metric
R24, R25: 0.05; R_0603_1608Metric
R30: 20K; R_0603_1608Metric
RV2: R_Potentiometer; TRIM_35WR10KLFTR

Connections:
+3V3: C32.1, IC1.15 (VDD), R23.1, R30.1; also elsewhere on the board
/Stepper_b/1A_b: IC1.24 (OUT1A); also elsewhere on the board
/Stepper_b/1B_b: IC1.21 (OUT1B); also elsewhere on the board
/Stepper_b/2A_b: IC1.26 (OUT2A); also elsewhere on the board
/Stepper_b/2B_b: IC1.1 (OUT2B); also elsewhere on the board
/Stepper_b/DIR_b: IC1.19 (DIR); also elsewhere on the board
/Stepper_b/MS1_b: IC1.9 (MS1); also elsewhere on the board
/Stepper_b/MS2_b: IC1.10 (MS2); also elsewhere on the board
/Stepper_b/MS3_b: IC1.11 (MS3); also elsewhere on the board
/Stepper_b/REF: IC1.17 (REF), J14.1, RV2.2
/Stepper_b/RST_b: IC1.12 (~RESET); also elsewhere on the board
/Stepper_b/SLP_b: IC1.14 (~SLEEP), R23.2; also elsewhere on the board
/Stepper_b/STEP_b: IC1.16 (STEP); also elsewhere on the board
/Stepper_b/VMM: C26.1, C27.1, C29.1, C31.1, IC1.22 (VBB1), IC1.28 (VBB2); also elsewhere on the board
GND: C26.2, C27.2, C29.2, C30.2, C32.2, IC1.3 (GND_1), IC1.18 (GND_2), IC1.29 (EP), J14.2, R21.1, R22.2, R24.2, R25.2, RV2.3; also elsewhere on the board
unnamed: C28.1, IC1.4 (CP1)
unnamed: C28.2, IC1.5 (CP2)
unnamed: C30.1, IC1.8 (VREG)
unnamed: C31.2, IC1.6 (VCP)
unnamed: IC1.2 (~ENABLE), R22.1
unnamed: IC1.13 (ROSC), R21.2
unnamed: IC1.23 (SENSE1), R25.1
unnamed: IC1.27 (SENSE2), R24.1
unnamed: R30.2, RV2.1

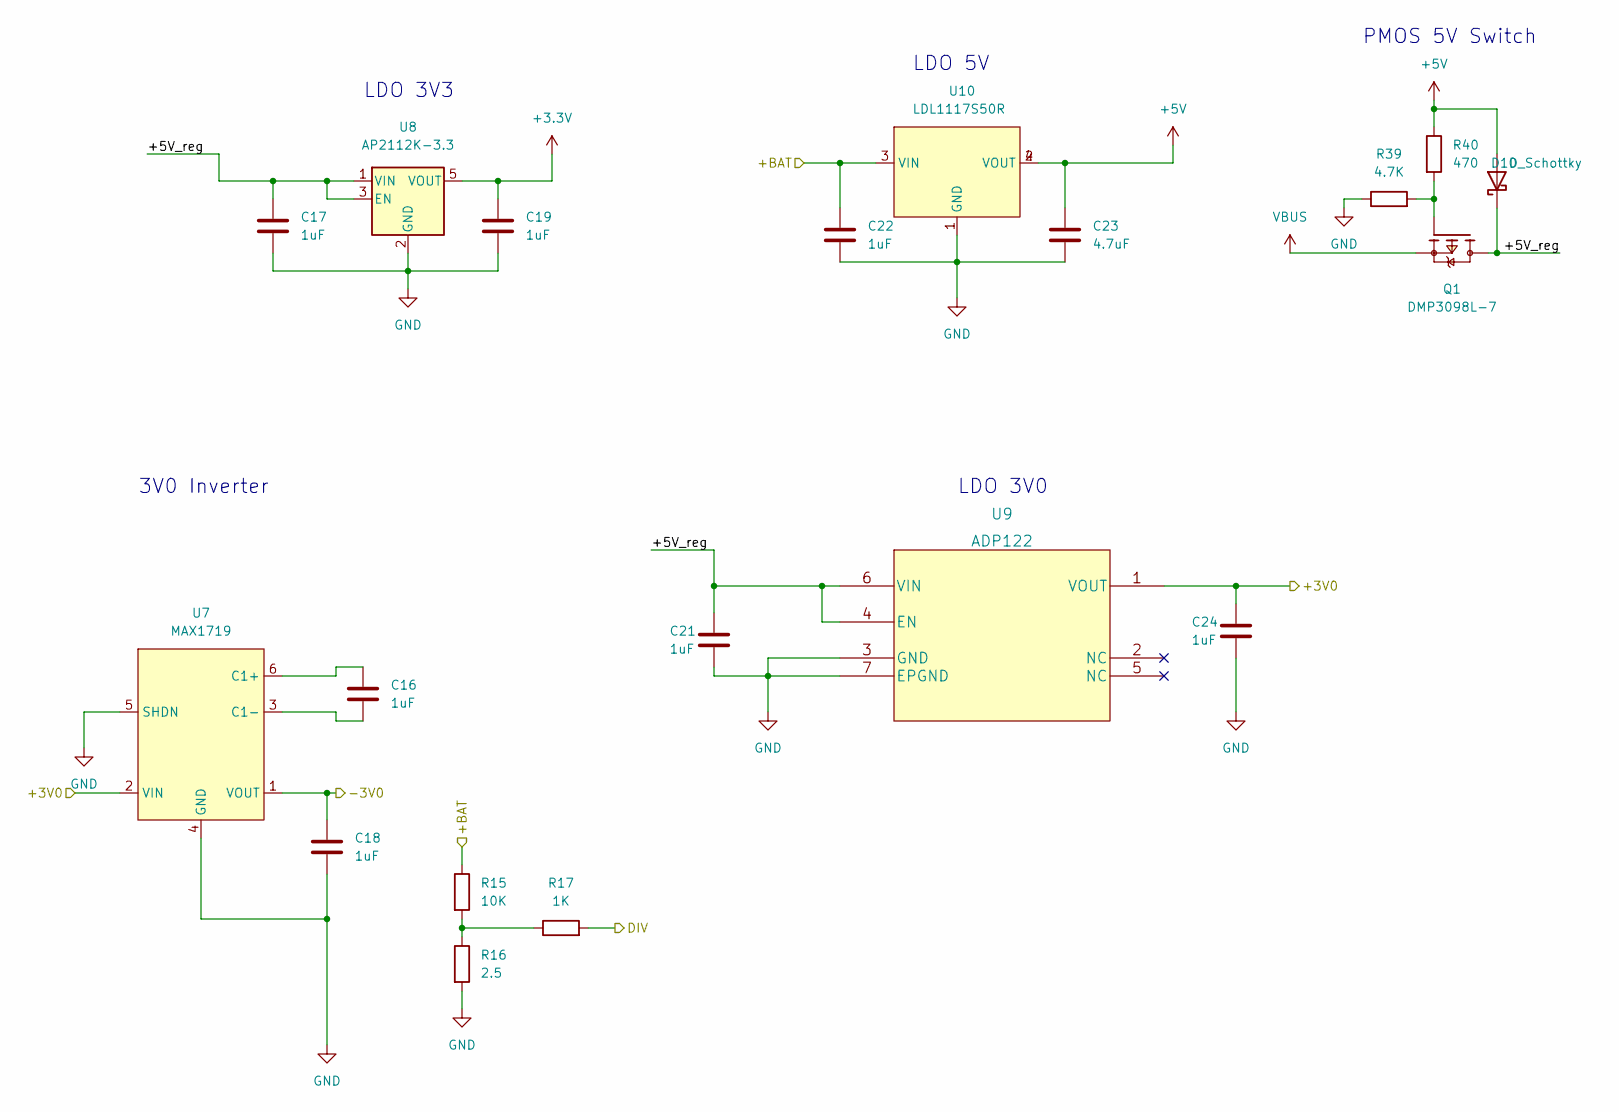
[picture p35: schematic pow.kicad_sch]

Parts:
C16, C17, C18, C19, C21, C22, C24: 1uF; C_0603_1608Metric
C23: 4.7uF; C_0603_1608Metric
D10: D_Schottky; DIOM4427X270N
Q1: DMP3098L-7; SOT91P240X110-3N; PARTREV 8 - 2
R15: 10K; R_0603_1608Metric
R16: 2.5; R_0603_1608Metric
R17: 1K; R_0603_1608Metric
R39: 4.7K; R_0603_1608Metric
R40: 470; R_0603_1608Metric
U7: MAX1719; SOT95P280X145-6N
U8: AP2112K-3.3; SOT95P285X140-5N
U9: ADP122; SON65P200X200X65-7N
U10: LDL1117S50R; SOT230P700X180-4N

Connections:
+3V3: C19.1, U8.5 (VOUT); also elsewhere on the board
+5V: C23.1, D10.A, R40.1, U10.2 (VOUT), U10.4 (VOUT); also elsewhere on the board
/Power/+3V0: C24.1, U7.2 (VIN), U9.1 (VOUT); also elsewhere on the board
/Power/+5V_reg: C17.1, C21.1, D10.C (K), Q1.3, U8.1 (VIN), U8.3 (EN), U9.4 (EN), U9.6 (VIN)
/Stepper_b/VMM: C22.1, R15.1, U10.3 (VIN); also elsewhere on the board
/TDS/RST: C18.1, U7.1 (VOUT); also elsewhere on the board
/V_DIV: R17.2; also elsewhere on the board
GND: C17.2, C18.2, C19.2, C21.2, C22.2, C23.2, C24.2, R16.2, R39.1, U7.4 (GND), U7.5 (SHDN), U8.2 (GND), U9.3 (GND), U9.7 (EPGND), U10.1 (GND); also elsewhere on the board
unnamed: C16.1, U7.6 (C1+)
unnamed: C16.2, U7.3 (C1-)
unnamed: Q1.1, R39.2, R40.2
unnamed: R15.2, R16.1, R17.1
VBUS: Q1.2; also elsewhere on the board

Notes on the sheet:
PMOS 5V Switch
LDO 5V
3V0 Inverter
LDO 3V3
LDO 3V0

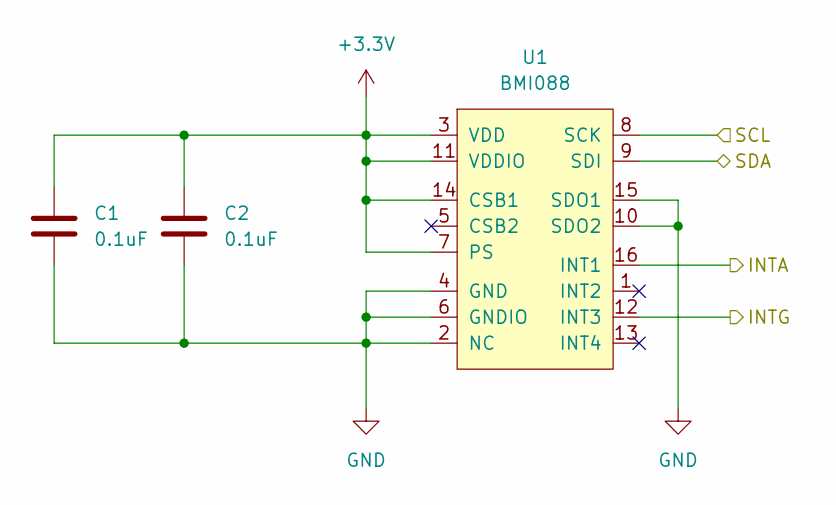
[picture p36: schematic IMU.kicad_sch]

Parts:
C1, C2: 0.1uF; C_0603_1608Metric
U1: BMI088; PQFN50P450X300X100-16N

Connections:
+3V3: C1.1, C2.1, U1.3 (VDD), U1.7 (PS), U1.11 (VDDIO), U1.14 (CSB1); also elsewhere on the board
/INT_ACC: U1.16 (INT1); also elsewhere on the board
/INT_GYR: U1.12 (INT3); also elsewhere on the board
/SCL: U1.8 (SCK); also elsewhere on the board
/SDA: U1.9 (SDI); also elsewhere on the board
GND: C1.2, C2.2, U1.2 (NC), U1.4 (GND), U1.6 (GNDIO), U1.10 (SDO2), U1.15 (SDO1); also elsewhere on the board

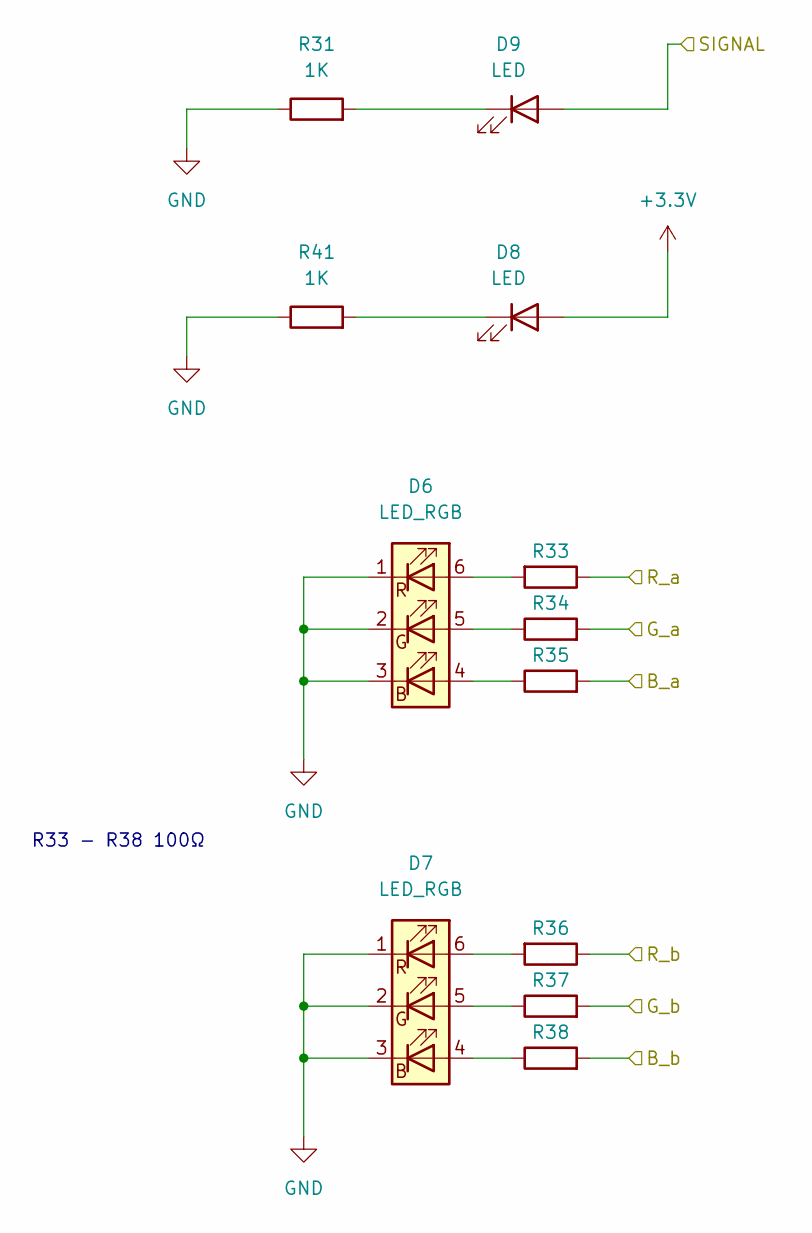
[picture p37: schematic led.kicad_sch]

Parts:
D6, D7: LED_RGB; LED_RGB_5050-6
D8, D9: LED; LED_0603_1608Metric
R31, R41: 1K; R_0603_1608Metric
R33, R35, R36, R38: R; R_0603_1608Metric
R34, R37: R_0603_1608Metric

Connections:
+3V3: D8.2 (A); also elsewhere on the board
/LEDs/B_a: R35.2; also elsewhere on the board
/LEDs/B_b: R38.2; also elsewhere on the board
/LEDs/G_a: R34.2; also elsewhere on the board
/LEDs/G_b: R37.2; also elsewhere on the board
/LEDs/R_a: R33.1; also elsewhere on the board
/LEDs/R_b: R36.1; also elsewhere on the board
/LEDs/SIGNAL: D9.2 (A); also elsewhere on the board
GND: D6.1 (RK), D6.2 (GK), D6.3 (BK), D7.1 (RK), D7.2 (GK), D7.3 (BK), R31.1, R41.1; also elsewhere on the board
unnamed: D6.4 (BA), R35.1
unnamed: D6.5 (GA), R34.1
unnamed: D6.6 (RA), R33.2
unnamed: D7.4 (BA), R38.1
unnamed: D7.5 (GA), R37.1
unnamed: D7.6 (RA), R36.2
unnamed: D8.1 (K), R41.2
unnamed: D9.1 (K), R31.2

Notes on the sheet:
R33 - R38 100Ω

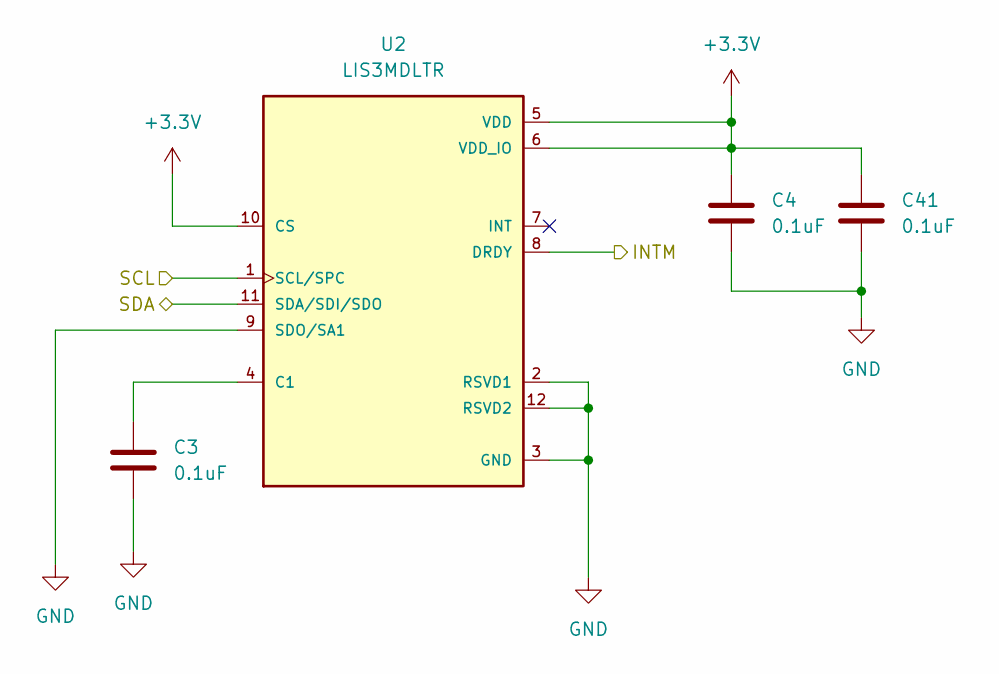
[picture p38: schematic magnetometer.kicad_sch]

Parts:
C3, C4, C41: 0.1uF; C_0603_1608Metric
U2: LIS3MDLTR; XDCR_LIS3MDLTR; PARTREV 6

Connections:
+3V3: C4.1, C41.1, U2.5 (VDD), U2.6 (VDD_IO), U2.10 (CS); also elsewhere on the board
/INT_MAG: U2.8 (DRDY); also elsewhere on the board
/SCL: U2.1 (SCL/SPC); also elsewhere on the board
/SDA: U2.11 (SDA/SDI/SDO); also elsewhere on the board
GND: C3.2, C4.2, C41.2, U2.2 (RSVD1), U2.3 (GND), U2.9 (SDO/SA1), U2.12 (RSVD2); also elsewhere on the board
unnamed: C3.1, U2.4 (C1)

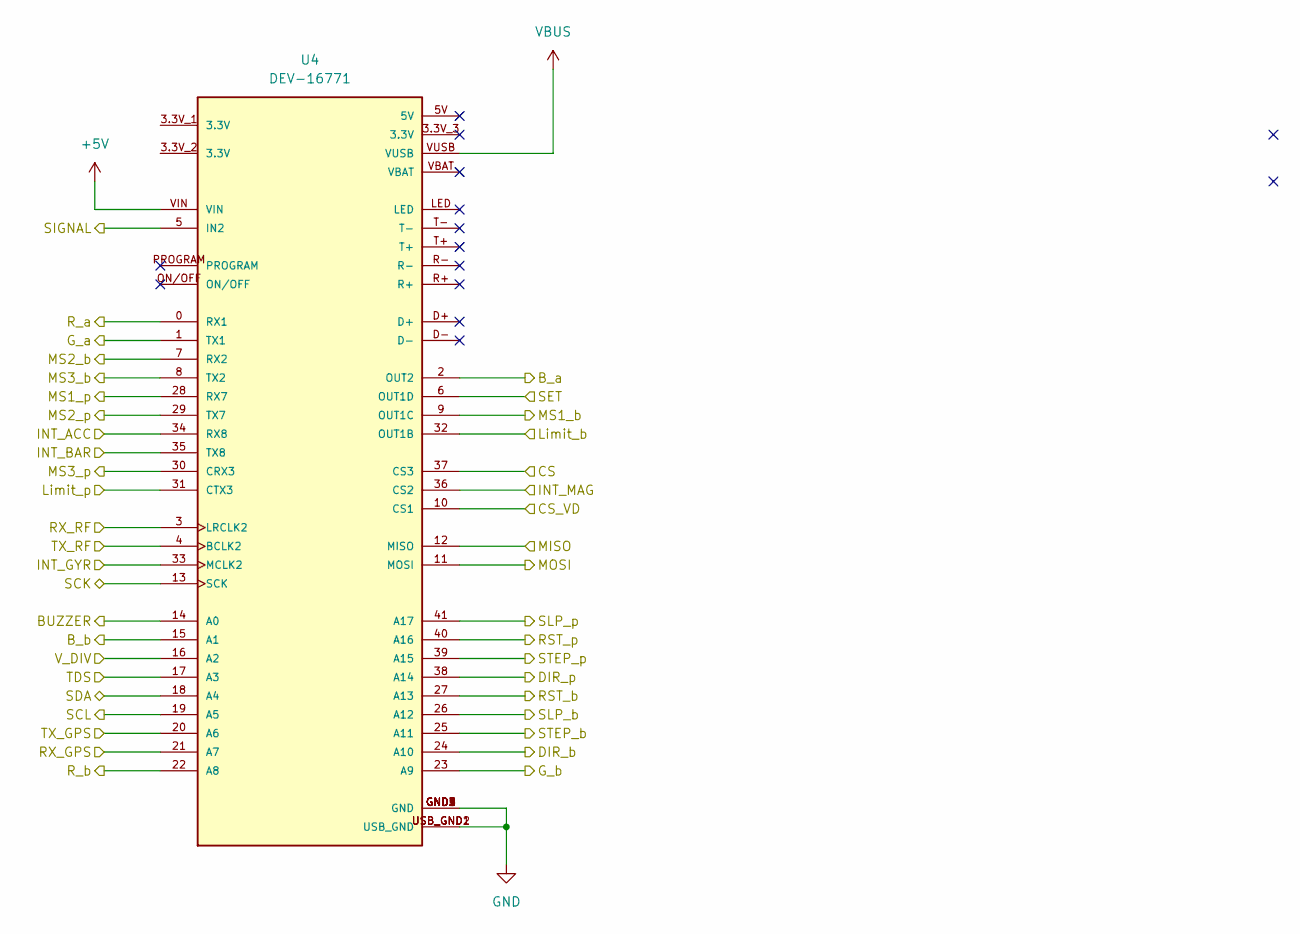
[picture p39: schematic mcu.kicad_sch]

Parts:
U4: DEV-16771; MODULE_DEV-16771; PARTREV 4.1

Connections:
+5V: U4.VIN; also elsewhere on the board
/CS: U4.37 (CS3); also elsewhere on the board
/CS_VD: U4.10 (CS1); also elsewhere on the board
/INT_ACC: U4.34 (RX8); also elsewhere on the board
/INT_BAR: U4.35 (TX8); also elsewhere on the board
/INT_GYR: U4.33 (MCLK2); also elsewhere on the board
/INT_MAG: U4.36 (CS2); also elsewhere on the board
/LEDs/B_a: U4.2 (OUT2); also elsewhere on the board
/LEDs/B_b: U4.15 (A1); also elsewhere on the board
/LEDs/G_a: U4.1 (TX1); also elsewhere on the board
/LEDs/G_b: U4.23 (A9); also elsewhere on the board
/LEDs/R_a: U4.0 (RX1); also elsewhere on the board
/LEDs/R_b: U4.22 (A8); also elsewhere on the board
/LEDs/SIGNAL: U4.5 (IN2); also elsewhere on the board
/MISO: U4.12 (MISO); also elsewhere on the board
/MOSI: U4.11 (MOSI); also elsewhere on the board
/RX_GPS: U4.21 (A7); also elsewhere on the board
/RX_RF: U4.3 (LRCLK2); also elsewhere on the board
/SCK: U4.13 (SCK); also elsewhere on the board
/SCL: U4.19 (A5); also elsewhere on the board
/SDA: U4.18 (A4); also elsewhere on the board
/SET: U4.6 (OUT1D); also elsewhere on the board
/Stepper_b1/DIR_b: U4.38 (A14); also elsewhere on the board
/Stepper_b1/MS1_b: U4.28 (RX7); also elsewhere on the board
/Stepper_b1/MS2_b: U4.29 (TX7); also elsewhere on the board
/Stepper_b1/MS3_b: U4.30 (CRX3); also elsewhere on the board
/Stepper_b1/RST_b: U4.40 (A16); also elsewhere on the board
/Stepper_b1/SLP_b: U4.41 (A17); also elsewhere on the board
/Stepper_b1/STEP_b: U4.39 (A15); also elsewhere on the board
/Stepper_b/DIR_b: U4.24 (A10); also elsewhere on the board
/Stepper_b/MS1_b: U4.9 (OUT1C); also elsewhere on the board
/Stepper_b/MS2_b: U4.7 (RX2); also elsewhere on the board
/Stepper_b/MS3_b: U4.8 (TX2); also elsewhere on the board
/Stepper_b/RST_b: U4.27 (A13); also elsewhere on the board
/Stepper_b/SLP_b: U4.26 (A12); also elsewhere on the board
/Stepper_b/STEP_b: U4.25 (A11); also elsewhere on the board
/TDS: U4.17 (A3); also elsewhere on the board
/TX_GPS: U4.20 (A6); also elsewhere on the board
/TX_RF: U4.4 (BCLK2); also elsewhere on the board
/Teensy41/BUZZER: U4.14 (A0); also elsewhere on the board
/Teensy41/Limit_b: U4.32 (OUT1B); also elsewhere on the board
/Teensy41/Limit_p: U4.31 (CTX3); also elsewhere on the board
/V_DIV: U4.16 (A2); also elsewhere on the board
GND: U4.GND1 (GND), U4.GND2 (GND), U4.GND3 (GND), U4.GND4 (GND), U4.GND5 (GND), U4.USB_GND1 (USB_GND), U4.USB_GND2 (USB_GND); also elsewhere on the board
VBUS: U4.VUSB; also elsewhere on the board

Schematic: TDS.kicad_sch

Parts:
C7: 1nF; C_0603_1608Metric
C8, C9, C14, C15: 0.1uF; C_0603_1608Metric
C10, C13: 1uF; C_0603_1608Metric
C11, C12: 4.7uF; C_0603_1608Metric
D1, D2, D3, D4, D5: 1N4148WS; D_SOD-323
J3: PROBE; TerminalBlock_MetzConnect_Type101_RT01602HBWC_1x02_P5.08mm_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
R1: 1M; R_0603_1608Metric
R4: 5.6K; R_0603_1608Metric
R5: 6.8K; R_0603_1608Metric
R6, R8: 100K; R_0603_1608Metric
R7, R9, R10, R11, R12, R13, R14: 10K; R_0603_1608Metric
U5: LM324A; SOIC127P600X175-14N
U6: CD4060BM; SOIC127P600X175-16N

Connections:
/Power/+3V0: C8.1, C11.1, C14.1, U5.4 (V+), U6.16 (VCC); also elsewhere on the board
/TDS: C13.1, D5.1 (K), R14.2; also elsewhere on the board
/TDS/RST: C9.1, C12.1, C15.1, U5.11 (V-), U6.8 (GND), U6.12 (RESET); also elsewhere on the board
GND: C8.2, C9.2, C10.2, C11.2, C12.2, C13.2, C14.2, C15.2, D5.2 (A), R1.2, U5.3 (+), U5.5 (+), U5.10 (+); also elsewhere on the board
unnamed: C7.1, R7.1, R8.1
unnamed: C7.2, U6.9 (EN1)
unnamed 62: C10.1, R13.2, R14.1; also elsewhere on the board
unnamed: D1.1 (K), D3.2 (A), U5.7
unnamed: D1.2 (A), R9.2, R11.1, U5.6 (-)
unnamed: D2.1 (K), D4.2 (A), U5.14
unnamed: D2.2 (A), R12.1, U5.13 (-)
unnamed 77: D3.1 (K), D4.1 (K), R11.2, R12.2, R13.1; also elsewhere on the board
unnamed: J3.1, R1.1, R4.1, U5.9 (-)
unnamed: J3.2, R5.1, U5.1
unnamed: R5.2, R6.1, U5.2 (-)
unnamed: R6.2, U6.7 (Q4)
unnamed: R7.2, U6.10 (EN2)
unnamed: R8.2, U6.11 (EN3)
unnamed: R4.2, R9.1, R10.1, U5.8
unnamed: R10.2, U5.12 (+)

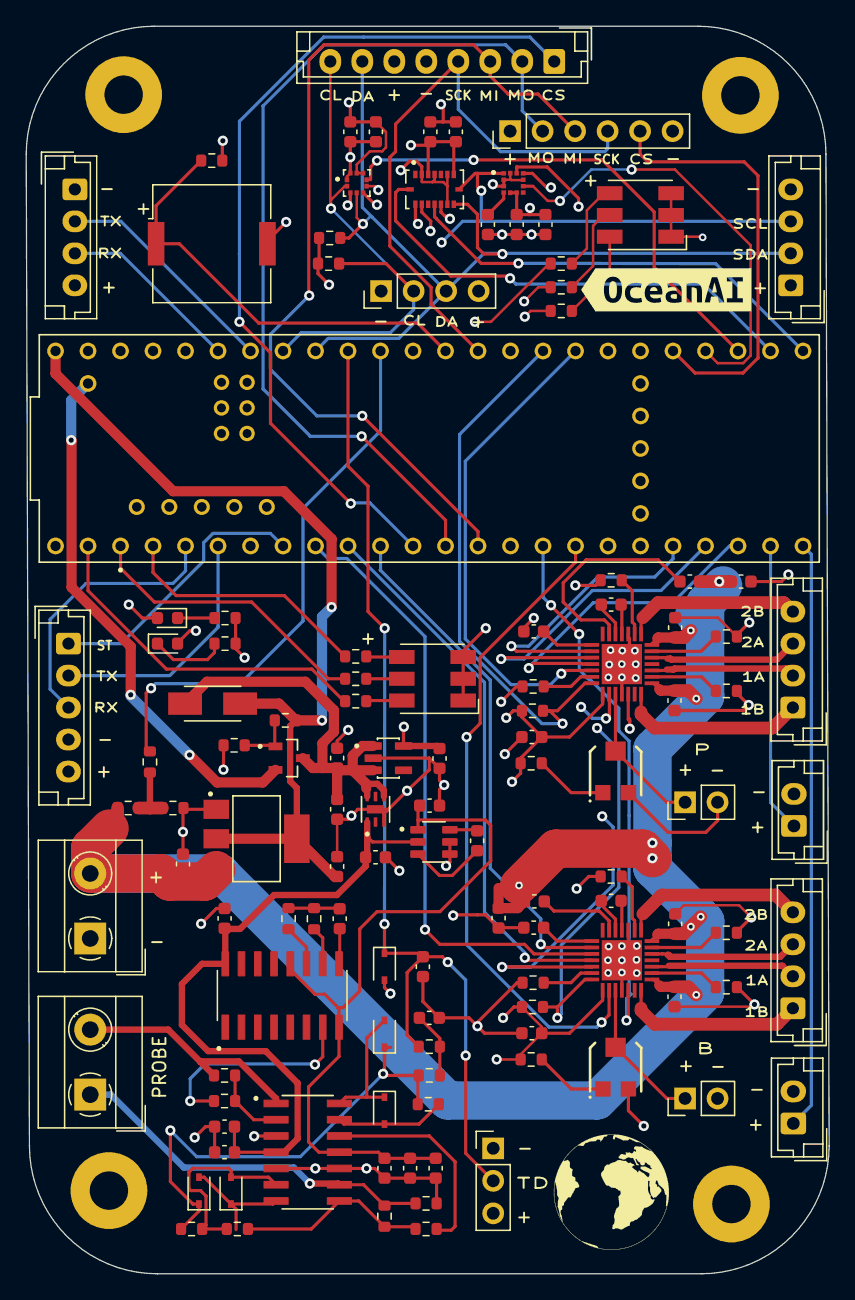
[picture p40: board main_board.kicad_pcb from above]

Board: 4 copper layers, 62.8 x 97.5 mm, 124 parts (0 on the bottom side), 107 nets.

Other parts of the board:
C20: 4.7uF; C_0603_1608Metric
C25, C33, C34, C36, C37: 0.1uF; C_0603_1608Metric
C35: 0.22uF; C_0603_1608Metric
IC2: A4988SETTR-T; QFN50P500X500X100-29N
J13: Conn_01x02; PinHeader_1x02_P2.54mm_Vertical
R19: 20K; R_0603_1608Metric
R20: 10K; R_0603_1608Metric
R26, R27: 100K; R_0603_1608Metric
R28, R29: 0.05; R_0603_1608Metric
RV1: R_Potentiometer; TRIM_35WR10KLFTR
kibuzzard-1: G***; kibuzzard-629BEB6E
locked: 10K; R_0603_1608Metric

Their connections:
+3V3: C37.1, IC2.15 (VDD), R19.1, R27.1; also elsewhere on the board
/Stepper_b1/1A_b: IC2.24 (OUT1A); also elsewhere on the board
/Stepper_b1/1B_b: IC2.21 (OUT1B); also elsewhere on the board
/Stepper_b1/2A_b: IC2.26 (OUT2A); also elsewhere on the board
/Stepper_b1/2B_b: IC2.1 (OUT2B); also elsewhere on the board
/Stepper_b1/DIR_b: IC2.19 (DIR); also elsewhere on the board
/Stepper_b1/MS1_b: IC2.9 (MS1); also elsewhere on the board
/Stepper_b1/MS2_b: IC2.10 (MS2); also elsewhere on the board
/Stepper_b1/MS3_b: IC2.11 (MS3); also elsewhere on the board
/Stepper_b1/REF: IC2.17 (REF), J13.1, RV1.2
/Stepper_b1/RST_b: IC2.12 (~RESET); also elsewhere on the board
/Stepper_b1/SLP_b: IC2.14 (~SLEEP), R27.2; also elsewhere on the board
/Stepper_b1/STEP_b: IC2.16 (STEP); also elsewhere on the board
/Stepper_b/VMM: C20.1, C25.1, C34.1, C36.1, IC2.22 (VBB1), IC2.28 (VBB2); also elsewhere on the board
GND: C20.2, C25.2, C34.2, C35.2, C37.2, IC2.3 (GND_1), IC2.18 (GND_2), IC2.29 (EP), J13.2, R20.1, R26.2, R28.2, R29.2, RV1.3; also elsewhere on the board
unnamed 62: locked.2; also elsewhere on the board
unnamed: C33.1, IC2.4 (CP1)
unnamed: C33.2, IC2.5 (CP2)
unnamed: C35.1, IC2.8 (VREG)
unnamed: C36.2, IC2.6 (VCP)
unnamed 77: locked.1; also elsewhere on the board
unnamed: IC2.2 (~ENABLE), R26.1
unnamed: IC2.13 (ROSC), R20.2
unnamed: IC2.23 (SENSE1), R29.1
unnamed: IC2.27 (SENSE2), R28.1
unnamed: R19.2, RV1.1

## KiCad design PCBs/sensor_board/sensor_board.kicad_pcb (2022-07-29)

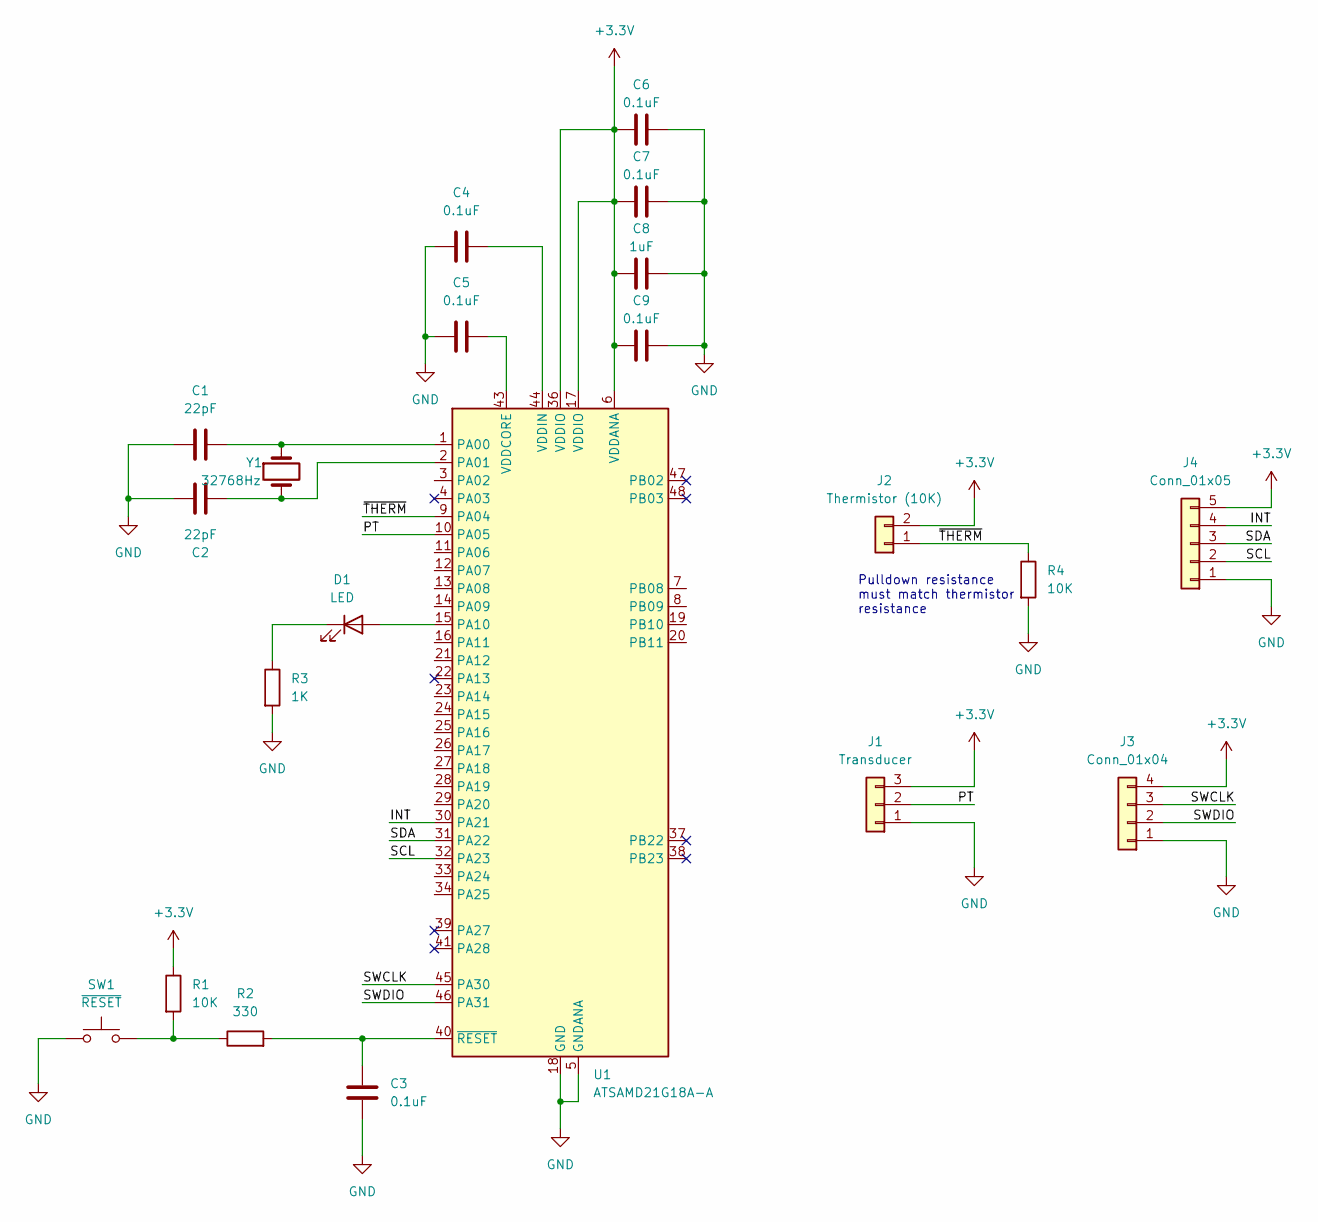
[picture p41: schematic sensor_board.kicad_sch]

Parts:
C1, C2: 22pF; C_0603_1608Metric
C3, C4, C5, C6, C7, C9: 0.1uF; C_0603_1608Metric
C8: 1uF; C_0603_1608Metric
D1: LED; LED_0603_1608Metric
J1: Transducer; PinHeader_1x03_P2.54mm_Vertical
J2: Thermistor (10K); PinHeader_1x02_P2.54mm_Vertical
J3: Conn_01x04; PinHeader_1x04_P2.54mm_Vertical
J4: Conn_01x05; PinHeader_1x05_P2.54mm_Vertical
R1, R4: 10K; R_0603_1608Metric
R2: 330; R_0603_1608Metric
R3: 1K; R_0603_1608Metric
SW1: ~{RESET}; PTS810SJG250SMTRLFS
U1: ATSAMD21G18A-A; TQFP-48_7x7mm_P0.5mm
Y1: 32768Hz; XTAL_ABS07-32.768KHZ-T

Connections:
+3V3: C6.1, C7.1, C8.1, C9.1, J1.3, J2.2, J3.4, J4.5, R1.1, U1.6 (VDDANA), U1.17 (VDDIO), U1.36 (VDDIO)
/INT: J4.4, U1.30 (PA21)
/PT: J1.2, U1.10 (PA05)
/SCL: J4.2, U1.32 (PA23)
/SDA: J4.3, U1.31 (PA22)
/SWCLK: J3.3, U1.45 (PA30)
/SWDIO: J3.2, U1.46 (PA31)
/~THERM: J2.1, R4.1, U1.9 (PA04)
GND: C1.1, C2.1, C3.2, C4.1, C5.1, C6.2, C7.2, C8.2, C9.2, J1.1, J3.1, J4.1, R3.2, R4.2, SW1.1, SW1.2, U1.5 (GNDANA), U1.18 (GND), U1.35 (GND), U1.42 (GND)
unnamed: C1.2, U1.1 (PA00), Y1.1
unnamed: C2.2, U1.2 (PA01), Y1.2
unnamed: C3.1, R2.2, U1.40 (~RESET)
unnamed: C4.2, U1.44 (VDDIN)
unnamed: C5.2, U1.43 (VDDCORE)
unnamed: D1.1 (K), R3.1
unnamed: D1.2 (A), U1.15 (PA10)
unnamed: R1.2, R2.1, SW1.3, SW1.4

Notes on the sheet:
Pulldown resistance must match thermistor resistance

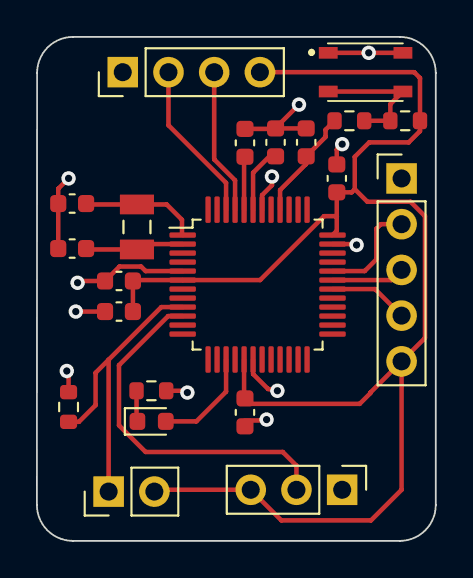
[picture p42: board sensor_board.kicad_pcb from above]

Board: 2 copper layers, 22.2 x 28.0 mm, 21 parts (0 on the bottom side), 17 nets.

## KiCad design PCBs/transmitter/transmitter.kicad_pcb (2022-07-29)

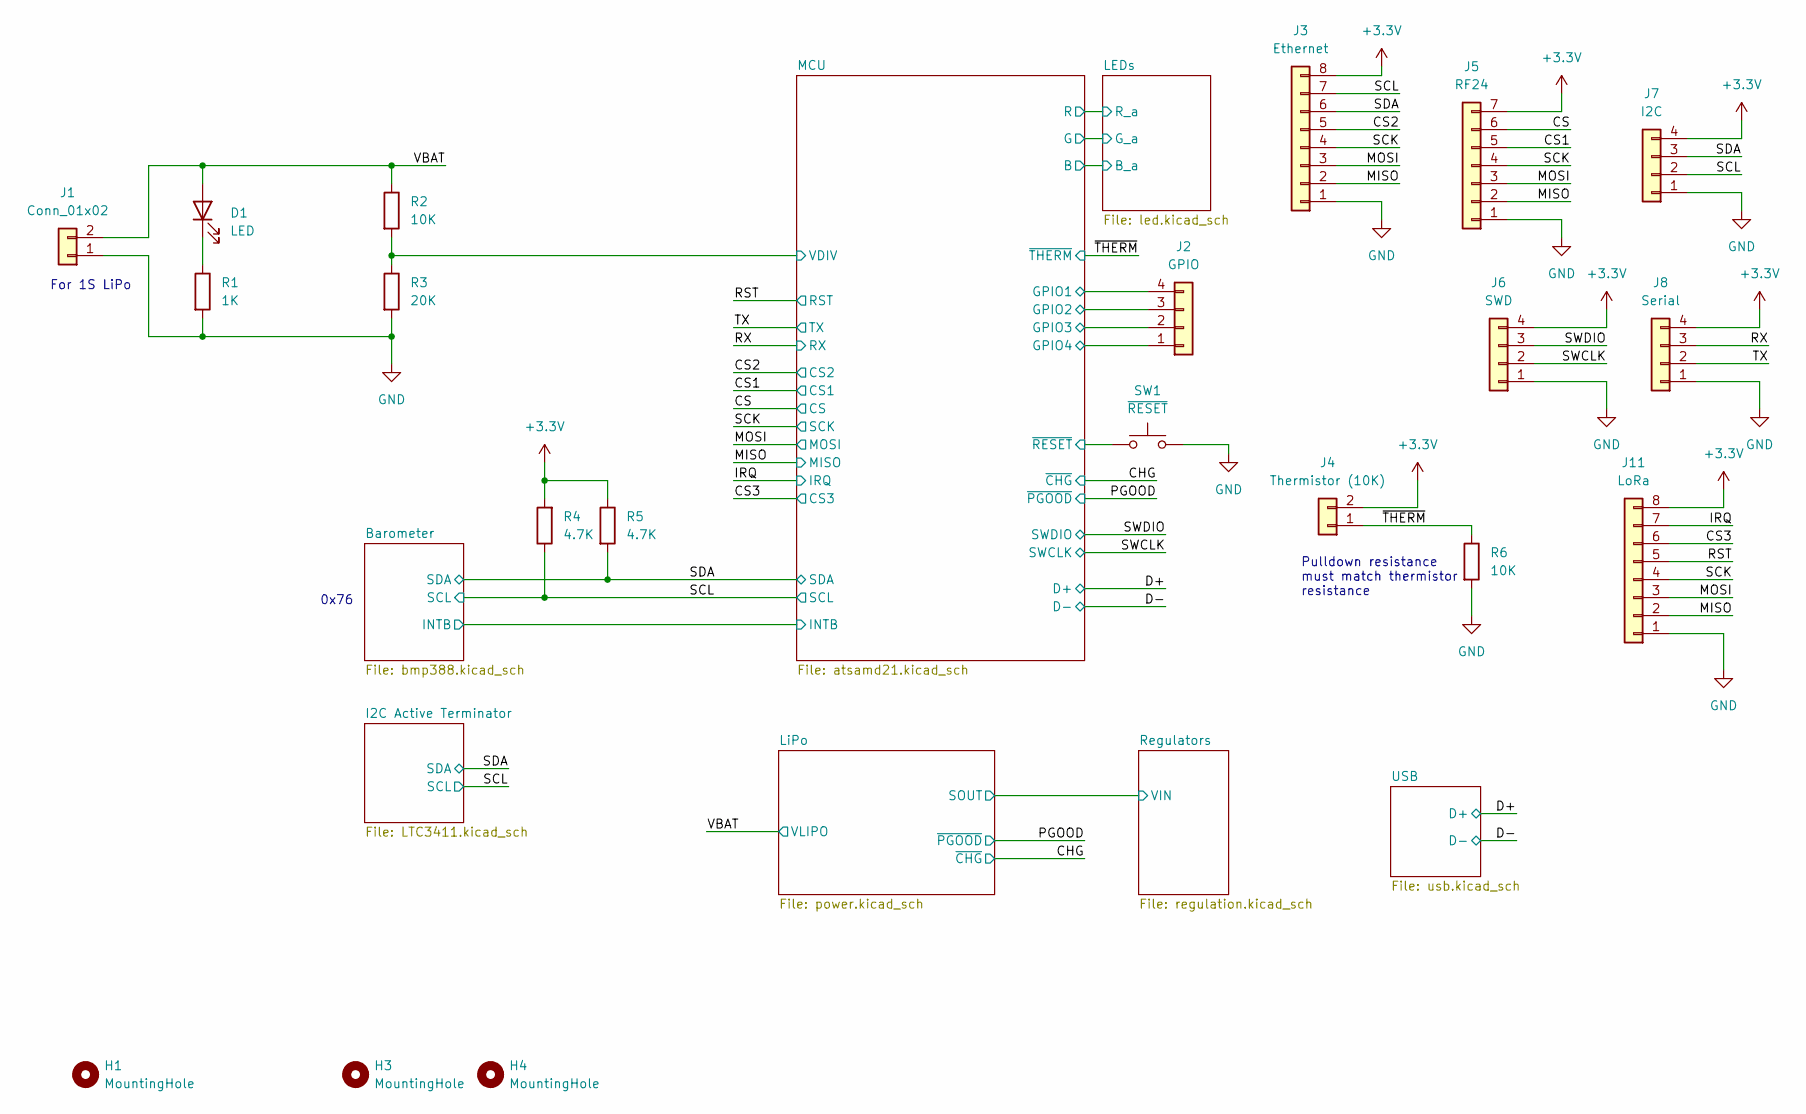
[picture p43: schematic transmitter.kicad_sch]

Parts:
D1: LED; LED_0603_1608Metric
H1, H3, H4: MountingHole; MountingHole_2mm
J1: Conn_01x02; JST_EH_B2B-EH-A_1x02_P2.50mm_Vertical
J2: GPIO; PinHeader_1x04_P2.54mm_Vertical
J3: Ethernet; PinHeader_1x08_P2.54mm_Vertical
J4: Thermistor (10K); PinHeader_1x02_P2.54mm_Vertical
J5: RF24; PinHeader_1x07_P2.54mm_Vertical
J6: SWD; PinHeader_1x04_P2.54mm_Vertical
J7: I2C; PinHeader_1x04_P2.54mm_Vertical
J8: Serial; PinHeader_1x04_P2.54mm_Vertical
J11: LoRa; PinHeader_1x08_P2.54mm_Vertical
R1: 1K; R_0603_1608Metric
R2, R6: 10K; R_0603_1608Metric
R3: 20K; R_0603_1608Metric
R4, R5: 4.7K; R_0603_1608Metric
SW1: ~{RESET}; PTS810SJG250SMTRLFS

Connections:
+3V3: J3.8, J4.2, J5.7, J6.4, J7.4, J8.4, J11.8, R4.2, R5.1; also elsewhere on the board
/CS: J5.6; also elsewhere on the board
/CS1: J5.5; also elsewhere on the board
/CS2: J3.5; also elsewhere on the board
/CS3: J11.6; also elsewhere on the board
/IRQ: J11.7; also elsewhere on the board
/MCU/GPIO1: J2.4; also elsewhere on the board
/MCU/GPIO2: J2.3; also elsewhere on the board
/MCU/GPIO3: J2.2; also elsewhere on the board
/MCU/GPIO4: J2.1; also elsewhere on the board
/MCU/VDIV: R2.2, R3.1; also elsewhere on the board
/MCU/~RESET: SW1.1, SW1.2; also elsewhere on the board
/MISO: J3.2, J5.2, J11.2; also elsewhere on the board
/MOSI: J3.3, J5.3, J11.3; also elsewhere on the board
/RST: J11.5; also elsewhere on the board
/RX: J8.3; also elsewhere on the board
/SCK: J3.4, J5.4, J11.4; also elsewhere on the board
/SCL: J3.7, J7.2, R4.1; also elsewhere on the board
/SDA: J3.6, J7.3, R5.2; also elsewhere on the board
/SWCLK: J6.2; also elsewhere on the board
/SWDIO: J6.3; also elsewhere on the board
/TX: J8.2; also elsewhere on the board
/VBAT: D1.2 (A), J1.2, R2.1; also elsewhere on the board
/~THERM: J4.1, R6.1; also elsewhere on the board
GND: J1.1, J3.1, J5.1, J6.1, J7.1, J8.1, J11.1, R1.2, R3.2, R6.2, SW1.3, SW1.4; also elsewhere on the board
unnamed: D1.1 (K), R1.1

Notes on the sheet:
For 1S LiPo
Pulldown resistance must match thermistor resistance
0x76


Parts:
C1, C2: 22pF; C_0603_1608Metric
C3, C4, C5, C6, C7, C9: 0.1uF; C_0603_1608Metric
C8: 1uF; C_0603_1608Metric
R7: 10K; R_0603_1608Metric
R8: 330; R_0603_1608Metric
U1: ATSAMD21G18A-A; TQFP-48_7x7mm_P0.5mm
Y1: 32768Hz; XTAL_ABS07-32.768KHZ-T

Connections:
+3V3: C6.1, C7.1, C8.1, C9.1, R7.1, U1.6 (VDDANA), U1.17 (VDDIO), U1.36 (VDDIO); also elsewhere on the board
/Barometer/INTB: U1.30 (PA21); also elsewhere on the board
/CHG: U1.9 (PA04); also elsewhere on the board
/CS: U1.8 (PB09); also elsewhere on the board
/CS1: U1.7 (PB08); also elsewhere on the board
/CS2: U1.28 (PA19); also elsewhere on the board
/CS3: U1.29 (PA20); also elsewhere on the board
/D+: U1.34 (PA25); also elsewhere on the board
/D-: U1.33 (PA24); also elsewhere on the board
/IRQ: U1.23 (PA14); also elsewhere on the board
/LEDs/B_a: U1.26 (PA17); also elsewhere on the board
/LEDs/G_a: U1.25 (PA16); also elsewhere on the board
/LEDs/R_a: U1.24 (PA15); also elsewhere on the board
/MCU/GPIO1: U1.11 (PA06); also elsewhere on the board
/MCU/GPIO2: U1.12 (PA07); also elsewhere on the board
/MCU/GPIO3: U1.13 (PA08); also elsewhere on the board
/MCU/GPIO4: U1.14 (PA09); also elsewhere on the board
/MCU/VDIV: U1.3 (PA02); also elsewhere on the board
/MCU/~RESET: R7.2, R8.1; also elsewhere on the board
/MISO: U1.21 (PA12); also elsewhere on the board
/MOSI: U1.19 (PB10); also elsewhere on the board
/PGOOD: U1.10 (PA05); also elsewhere on the board
/RST: U1.27 (PA18); also elsewhere on the board
/RX: U1.16 (PA11); also elsewhere on the board
/SCK: U1.20 (PB11); also elsewhere on the board
/SCL: U1.32 (PA23); also elsewhere on the board
/SDA: U1.31 (PA22); also elsewhere on the board
/SWCLK: U1.45 (PA30); also elsewhere on the board
/SWDIO: U1.46 (PA31); also elsewhere on the board
/TX: U1.15 (PA10); also elsewhere on the board
/~THERM: U1.47 (PB02); also elsewhere on the board
GND: C1.1, C2.1, C3.2, C4.1, C5.1, C6.2, C7.2, C8.2, C9.2, U1.5 (GNDANA), U1.18 (GND), U1.35 (GND), U1.42 (GND); also elsewhere on the board
unnamed: C1.2, U1.1 (PA00), Y1.1
unnamed: C2.2, U1.2 (PA01), Y1.2
unnamed: C3.1, R8.2, U1.40 (~RESET)
unnamed: C4.2, U1.44 (VDDIN)
unnamed: C5.2, U1.43 (VDDCORE)


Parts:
C19: 0.1uF; C_0603_1608Metric
R23: 10K; R_0603_1608Metric
U5: LTC4311CSC6#TRPBF; LTC4311CSC6_TRPBF; MANUFACTURER_PART_NUMBER ltc4311csc6#pbf

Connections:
+3V3: C19.1, R23.2, U5.1 (VCC); also elsewhere on the board
/I2C Active Terminator/EN: R23.1, U5.3 (ENABLE)
/SCL: U5.6 (BUS1); also elsewhere on the board
/SDA: U5.4 (BUS2); also elsewhere on the board
GND: C19.2, U5.2 (GND_2), U5.5 (GND); also elsewhere on the board


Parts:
C15, C16: 0.47uF; C_0603_1608Metric
D5: D_Schottky; 1N4148
Q1: DMP3098L-7; DMP3098L; PARTREV 8 - 2
R16: 4.7K; R_0603_1608Metric
R17: 470; R_0603_1608Metric
U3: LP5900SD-3.3/NOPB; LP5900SD-3.3_NOPB; PARTREV R

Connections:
+3V3: C16.1, U3.1 (OUT); also elsewhere on the board
/LiPo/SOUT: D5.A, R17.2; also elsewhere on the board
/Regulators/+5V_reg: C15.1, D5.C (K), Q1.3, U3.4 (EN), U3.6 (IN)
GND: C15.2, C16.2, R16.2, U3.3 (GND), U3.7 (EXP); also elsewhere on the board
unnamed: Q1.1, R16.1, R17.1
VBUS: Q1.2; also elsewhere on the board

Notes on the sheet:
3.3V LDO


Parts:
D7: LED_RGB; LED_RGB_5050-6
R20, R21, R22: 100; R_0603_1608Metric

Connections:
/LEDs/B_a: R22.2; also elsewhere on the board
/LEDs/G_a: R21.2; also elsewhere on the board
/LEDs/R_a: R20.2; also elsewhere on the board
GND: D7.1 (RK), D7.2 (GK), D7.3 (BK); also elsewhere on the board
unnamed: D7.4 (BA), R22.1
unnamed: D7.5 (GA), R21.1
unnamed: D7.6 (RA), R20.1


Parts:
C17, C18: 0.1uF; C_0603_1608Metric
U4: BMP388; bmp388

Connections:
+3V3: C17.1, C18.1, U4.1 (VDDIO), U4.6 (CSB), U4.10 (VDD); also elsewhere on the board
/Barometer/INTB: U4.7 (INT); also elsewhere on the board
/SCL: U4.2 (SCK); also elsewhere on the board
/SDA: U4.4 (SDI); also elsewhere on the board
GND: C17.2, C18.2, U4.3 (VSS), U4.5 (SDO), U4.8 (VSS), U4.9 (VSS); also elsewhere on the board


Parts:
D6: SK34A; D_SMA
J10: 1054550101; MOLEX_1054550101; PARTREV A2
R18, R19: 5.1K; R_0603_1608Metric

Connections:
/D+: J10.A6 (D+_A), J10.B6 (D+_B); also elsewhere on the board
/D-: J10.A7 (D-_A), J10.B7 (D-_B); also elsewhere on the board
GND: J10.A1 (GND), J10.A12 (GND), J10.B1 (GND), J10.B12 (GND), R18.2, R19.2; also elsewhere on the board
unnamed: D6.2 (A), J10.A4 (VBUS), J10.A9 (VBUS), J10.B4 (VBUS), J10.B9 (VBUS)
unnamed: J10.A5 (CC1), R18.1
unnamed: J10.B5 (CC2), R19.1
VBUS: D6.1 (K); also elsewhere on the board


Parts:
C10, C11, C12, C13, C14: 10uF; C_0603_1608Metric
D2: SK34A; D_SMA
D3, D4: LED; LED_0603_1608Metric
J9: SOLAR; JST_EH_B2B-EH-A_1x02_P2.50mm_Vertical
R9, R10, R13, R14, R15: 10K; R_0603_1608Metric
R11, R12: 1K; R_0603_1608Metric
U2: BQ24074RGT; VQFN-16-1EP_3x3mm_P0.5mm_EP1.6x1.6mm

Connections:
+3V3: D3.2 (A), D4.2 (A); also elsewhere on the board
/CHG: R15.2, U2.9 (~CHG); also elsewhere on the board
/LiPo/SOUT: C12.1, C13.1, C14.1, U2.5 (EN2), U2.10 (OUT), U2.11 (OUT); also elsewhere on the board
/PGOOD: R14.1, U2.7 (~PGOOD); also elsewhere on the board
/VBAT: C10.1, C11.1, U2.2 (BAT), U2.3 (BAT); also elsewhere on the board
GND: C10.2, C11.2, C12.2, C13.2, C14.2, J9.1, R9.1, R10.1, R11.1, R12.1, R13.1, U2.6 (EN1), U2.8 (VSS), U2.14 (TMR), U2.17 (VSS); also elsewhere on the board
unnamed: D2.2 (A), J9.2
unnamed: D3.1 (K), R14.2
unnamed: D4.1 (K), R15.1
unnamed: R9.2, U2.15 (ITERM)
unnamed: R10.2, U2.4 (~CE)
unnamed: R11.2, U2.12 (ILIM)
unnamed: R12.2, U2.16 (ISET)
unnamed: R13.2, U2.1 (TS)
VBUS: D2.1 (K), U2.13 (IN); also elsewhere on the board



Board: 4 copper layers, 34.0 x 65.0 mm, 71 parts (6 on the bottom side), 58 nets.

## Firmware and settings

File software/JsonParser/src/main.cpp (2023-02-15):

#include <iostream>
#include <fstream>
#include <sstream>
#include <string>
#include <algorithm>
#include <vector>
#include <thread>
#include <cmath>
#include "../include/json.hpp"


void read_lines(std::ifstream &file, std::vector<std::string> &json)
{
    int current_line = 0;
    int index = 0;
    std::string output;
    std::string combined;

    while(std::getline(file, output))
    {
        if(!output.empty())
        {
            json.push_back(output);
        }
    }
}

void to_csv(std::string json_line, std::ofstream &csv, char delimiter)
{
    nlohmann::json json = nlohmann::json::parse(json_line, nullptr, false, true);
    csv << json["time"] << delimiter;
    for(int i = 0; i < json["sys_data"].size(); i++)
    {
        csv << json["sys_data"][i] << delimiter;
    }
    
    for(int i = 0; i < json["location_data"].size(); i++)
    {
        csv << json["location_data"][i] << delimiter;
    }

    for(int i = 0; i < json["baro_data"].size(); i++)
    {
        csv << json["baro_data"][i] << delimiter;
    }

    for(int i = 0; i < json["IMU_data"].size(); i++)
    {
        csv << json["IMU_data"][i] << delimiter;
    }

    for(int i = 0; i < json["external_data"].size(); i++)
    {
        csv << json["external_data"][i] << delimiter;
    }

    for(int i = 0; i < json["step_data"].size(); i++)
    {
        csv << json["step_data"][i] << delimiter;
    }

    for(int i = 0; i < json["optics"].size(); i++)
    {
        csv << json["optics"][i] << delimiter;
    }
    csv << "\n";
}

void thread_convert(std::vector<std::string> &json, std::ofstream &csv, char delimiter, unsigned long start, unsigned long end)
{
    for(unsigned long i = start; i < end; i++)
    {
        to_csv(json[i], csv, delimiter);

        //Print progress
        if(i % 1000 == 0)
        {
            std::cout << "Progress: " << i << std::endl;
        }
    }
}

int main(int argc, char const *argv[])
{
    std::string input_file(argv[1]);

    std::string output_file = input_file.substr(0, input_file.find_last_of(".")) + ".csv";
    std::ifstream json_input(input_file);

    if(!json_input.is_open())
    {
        std::cout << "Error opening file" << std::endl;
        return 1;
    }
    else
    {
        std::vector<std::string> json_vector;
        read_lines(json_input, json_vector);

        std::ofstream csv(output_file);
        constexpr char delimiter = ',';
        csv << "time(ns),loop_time(hz),system_state,delta_time(s),sd_capacity(bytes),r_voltage,f_voltage,clockspeed(hz),internal_temp(°C),";
        csv << "lat(deg),lon(deg),"
        csv << "bmp_pres(atm),bmp_temp(°C),";
        csv << "bmi_temp(°C),rax(m/s^2),ray(m/s^2),raz(m/s^2),wfax(m/s^2),wfay(m/s^2),wfaz(m/s^2),velx(m/s),vely(m/s),velz(m/s),posx(m),posy(m),posz(m),";
        csv << "rgx(rad/s),rgy(rad/s),rgz(rad/s),ori_x(deg),ori_y(deg),ori_z(deg),q_w,q_x,q_y,q_z,";
        csv << "rmagx(uT),rmagy(uT),rmagz(uT),fmagx(uT),fmagy(uT),fmagz(uT),";
        csv << "rTDS,fTDS,r_ext_pres,f_ext_pres,depth,r_ext_temp,f_ext_temp,";
        csv << "dive_limit,dive_homed,dive_current_position,dive_current_position_mm,dive_target_position,dive_target_position_mm,dive_speed,dive_acceleration,dive_maxspeed,";
        csv << "pitch_limit,pitch_homed,pitch_current_position,pitch_current_position_mm,pitch_target_position,pitch_target_position_mm,pitch_speed,pitch_acceleration,pitch_maxspeed,";
        csv << "cap_time(ms),save_time(ms),fifo_length(bytes)\n";

        unsigned long json_elements = json_vector.size() - 1;

        std::cout << "Number of elements: " << json_elements << std::endl;

        int num_available_threads = std::thread::hardware_concurrency();

        std::cout << "Number of threads: " << num_available_threads << std::endl;

        //Divide the number of elements by the number of threads. Round down
        unsigned long elements_per_thread = std::floor(json_elements / num_available_threads);
        int remainder = json_elements % num_available_threads;

        std::cout << "Elements per thread: " << elements_per_thread << std::endl;

        for(int i = 0; i < num_available_threads; i++)
        {
            unsigned long start = i * elements_per_thread;
            unsigned long end = start + elements_per_thread;
            if(i == num_available_threads - 1)
            {
                end += remainder;
            }
            std::thread t(thread_convert, std::ref(json_vector), std::ref(csv), delimiter, start, end);
            t.join();
        }

        csv.close();
        json_input.close();

        std::cout << "Done" << std::endl;
        
    }
}

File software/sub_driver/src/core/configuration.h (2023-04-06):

/**
 * @file configuration.h
 * @author Daniel Kim
 * @brief configurations for the system
 * @version 0.1
 * @date 2022-12-25
 *
 * @copyright Copyright (c) 2022 OceanAI (https://github.com/daniel360kim/OceanAI)
 *
 */

#ifndef CONFIGURATION_H
#define CONFIGURATION_H

#include <cmath>

#include "timer.h"
#include "../Data/logged_data.h"

/**
 * Debug funciontality for the system
 * DEBUG saves internal debug messages internally
 * LIVE_DEBUG sends internal debug messages to the Serial monitor
 */
#define DEBUG_ON false
#define LIVE_DEBUG false

/**
 * HITL functionality for the system
 * Set HITL_LOOP to true to reloop through the HITL data
 */
#define HITL_ON true
#define HITL_LOOP true

/**
 * UI functionality for the system
 * Make sure there are no serial outputs while UI is on
 */
#define UI_ON true

#if UI_ON && !HITL_ON
#warning UI requires HITL to be enabled.
#endif

#define PRINT_DATA false //prints out logged data as JSON

#if UI_ON && LIVE_DEBUG 
#warning UI and Debug outputs will collide. Disable one of them.
#endif

#if UI_ON && PRINT_DATA
#warning UI and Data outputs will collide. Disable one of them.
#endif

#define SD_ON false

#define OPTICS_ON false

/**
 * @brief Mission duration setting to preallocate space in microSD
 * 
 */
namespace MissionDuration
{
    constexpr uint16_t days = 0;
    constexpr uint16_t hours = 0;
    constexpr uint32_t minutes = 0;
    constexpr uint32_t seconds = 5000;

    constexpr uint64_t mission_time = ((uint64_t)(days * (uint64_t)8.64e+13) + (uint64_t)(hours * (uint64_t)3.6e+12) + (uint64_t)(minutes * (uint64_t)6e+10) + (uint64_t)(seconds * (uint64_t)1e+9));
}

namespace CPU
{
    /**
     * @brief thresholds for throttling in degrees Celsius
     * Lowers clock speed when temperature is above OVERTEMP_THRESHOLD
     * Raises clock speed when temperature is below UNDERTEMP_THRESHOLD
     */
    constexpr int OVERTEMP_THRESHOLD = 80;
    constexpr int UNDERTEMP_THRESHOLD = 70;

    /**
     * @brief clock speeds in Hz
     * Raises clock speed to HIGH_CLOCKSPEED when temperature is below UNDERTEMP_THRESHOLD
     * Lowers clock speed to LOW_CLOCKSPEED when temperature is above OVERTEMP_THRESHOLD
     */
    constexpr int HIGH_CLOCKSPEED = 528000000;
    constexpr int LOW_CLOCKSPEED = 350000000;

    /**
     * @brief interval for logging CPU info
     */
    constexpr int CPU_INFO_LOG_INTERVAL = HZ_TO_NS(1);
};

namespace Sensors
{
    constexpr Angles_3D<double> mag_bias = {0.36, 0.39, 0.49}; // in uT: set in mag calibration script
}


    constexpr int SEND_INTERVAL = HZ_TO_NS(100); //how often data is sent to the GUI


namespace Logging
{
    constexpr int LOG_INTERVAL = HZ_TO_NS(30);
    constexpr int BYTES_PER_LOG = 1536; // bytes per log
    constexpr unsigned long long FLUSH_INTERVAL = SEC_TO_NS(30ULL); // flush every 30 seconds
    constexpr unsigned long long CAPACITY_UPDATE_INTERVAL = SEC_TO_NS(360);// update capacity every 6 minutes
}

namespace Mechanics
{
    constexpr int BUOYANCY_DEFAULT_STEPPER_SPEED = 800; // default speed for stepper motor
    constexpr int BUOYANCY_DEFAULT_STEPPER_ACCELERATION = 500; // default acceleration for stepper motor

    constexpr int PITCH_DEFAULT_STEPPER_SPEED = 1000; // default speed for stepper motor
    constexpr int PITCH_DEFAULT_STEPPER_ACCELERATION = 500; // default acceleration for stepper motor
    
    constexpr int MIN_PULSE_WIDTH = 1; // minimum pulse width in microseconds for stepper motor
}

#endif

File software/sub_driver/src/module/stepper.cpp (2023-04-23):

#include "stepper.h"
#include "../core/configuration.h"

#include <cmath>

namespace Mechanics
{
    /**
     * @brief Construct a new Stepper:: Stepper object
     * Also intializes GPIO
     * @param pins pins of the stepper driver
     * @param resolution initial resolution
     * @param properties properties of the stepper structure
     */
    Stepper::Stepper(StepperPins pins, Resolution resolution, StepperProperties properties) : AccelStepper(1, pins.STP, pins.DIR)
    {
        this->pins = pins;
        this->properties = properties;

        pinMode(pins.MS1, OUTPUT);
        pinMode(pins.MS2, OUTPUT);
        pinMode(pins.ERR, INPUT);

        limit.begin(pins.limit);

        setResolution(resolution);

        steps_per_mm = properties.halves_length / properties.carriage_length;
    }


    /**
     * @brief Configures GPIO to control resolution of TMC2208 stepper driver
     * 
     * @param resolution resolution to set
     */
    void Stepper::setResolution(Resolution resolution)
    {
        this->resolution = resolution;
        switch (resolution)
        {
        case Resolution::HALF:
            digitalWrite(pins.MS1, LOW);
            digitalWrite(pins.MS2, HIGH);
            res_multiplier = 2;
        
            break;
        case Resolution::QUARTER:
            digitalWrite(pins.MS1, HIGH);
            digitalWrite(pins.MS2, LOW);
            res_multiplier = 4;

            setMaxSpeed(maxSpeed() / res_multiplier);
            setSpeed(speed() / res_multiplier);

            break;
        case Resolution::EIGHTH:
            digitalWrite(pins.MS1, LOW);
            digitalWrite(pins.MS2, LOW);
            res_multiplier = 8;

            setMaxSpeed(maxSpeed() / res_multiplier);
            setSpeed(speed() / res_multiplier);

            break;
        case Resolution::SIXTEENTH:
            digitalWrite(pins.MS1, HIGH);
            digitalWrite(pins.MS2, HIGH);
            res_multiplier = 16;

            setMaxSpeed(maxSpeed() / res_multiplier);
            setSpeed(speed() / res_multiplier);

            break;
        }
    }

    /**
     * @brief Calibrates the stepper motor
     * Must set stepper speeds and accelerations before calling this
     * 
     */
    bool Stepper::calibrate()
    {
        moveTo(100000000); //move to end of rail

        if(limit.state() == true)
        {
            moveTo(0);
            setCurrentPosition(0);
            update();
            calibrated = true;
            return true;
        }
        else
        {
            return false;
        }
    }

    void Stepper::setSpeeds(double speed, double acceleration)
    {
        setSpeed(speed);
        setMaxSpeed(speed);
        setAcceleration(acceleration);
    }


    /**
     * @brief After limit switch is pressed once, it goes back and slowly eases back in
     * For further precision
     * 
     */
    void Stepper::recheckLimit()
    {
        setCurrentPosition(0);
        move(-1000);
        while(currentPosition() != 1000)
        {
            run();
        }
        
        setResolution(Resolution::EIGHTH);

        move(100000000);
        uint64_t start = millis();
        while(limit.state() == false)
        {
            if(millis() - start > 10000)
            {
                return;
            }
            run();
        }

        setCurrentPosition(0);
    }

    /**
     * @brief Overhead to account for resolution changes
     * 
     * @return double 
     */
    double Stepper::currentPosition_mm()
    {
        return currentPosition() / steps_per_mm;
    }

    /**
     * @brief Move in mm. Due to floating point precision, small errors will integrate and cause drit
     * Use move_steps() instead
     * 
     * @return double 
     */
    double Stepper::targetPosition_mm()
    {
        return targetPosition() / steps_per_mm;
    }

    /**
     * @brief accounts for resolution changes
     * 
     * @param absolute 
     */
    void Stepper::goTo(long absolute)
    {
        if(resolution == Resolution::HALF)
        {
            move(absolute);
            return;
        }
        else if(resolution == Resolution::QUARTER)
        {
            absolute /= 2;
            pos_multiplier = 2;
        }
        else if(resolution == Resolution::EIGHTH)
        {
            absolute *= 4;
            pos_multiplier = 0.25;
        }
        else if(resolution == Resolution::SIXTEENTH)
        {
            absolute *= 8;
            pos_multiplier = 0.125;
        }
        else
        {
            return;
        }
        move(absolute);
    }

    /**
     * @brief Moves in mm. Use move() instead when you can
     * Floating point inprecision adds up and causes drift
     * 
     * @param mm 
     */
    void Stepper::move_mm(int mm)
    {
        goTo(mm * steps_per_mm);
    }

    /**
     * @brief Must call in loop to update
     * 
     * @return true all is good!
     * @return false all is not good
     */
    bool Stepper::update()
    {
        if(digitalRead(pins.ERR) == HIGH) //TMC2208 is reporting an error :(
        {
            return false; 
        }
        else
        {
            run();
            return true;
        }
    }

    //END OF STEPPER

    //BEGINNING OF BUOYANCY

    /**
     * @brief pulls in water to sink. WILL NOT RUN; MUST CALL an updating function
     * 
     */
    void Buoyancy::sink()
    {
        moveTo(properties.halves_length); //go to the other side of the carriage

        sinking = true;
        rising = false;
    }

    /**
     * @brief pushes all water out to float. WILL NOT RUN; MUST CALL an updating function
     * 
     */
    void Buoyancy::rise()
    {
        moveTo(-1 * properties.halves_length); //moves to the very end of the carriage

        sinking = false;
        rising = true;
    }

    void Buoyancy::rise(long half_steps)
    {
        move(-1 * half_steps);

        sinking = false;
        rising = true;
    }


    void Buoyancy::logToStruct(LoggedData &data)
    {
        data.dive_stepper.current_position = currentPosition();
        data.dive_stepper.target_position = targetPosition();

        data.dive_stepper.current_position_mm = currentPosition_mm();
        data.dive_stepper.target_position_mm = targetPosition_mm();

        data.dive_stepper.limit_state = limit.state();

        data.dive_stepper.speed = speed();
        data.dive_stepper.max_speed = maxSpeed();
        data.dive_stepper.acceleration = acceleration();
    }

    void Pitch::runPitch(TransportManager::Commands &commands, CurrentState state, double buoyancy_position)
    {
        if(commands.auto_pitch != 0)
        {
            manualMode(commands);
        }
        else
        {
            autoMode(state, buoyancy_position);
        }
    }

    void Pitch::runPitch(CurrentState state, double buoyancy_position)
    {
        autoMode(state, buoyancy_position);
    }
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

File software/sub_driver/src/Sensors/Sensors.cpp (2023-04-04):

/**
 * @file Sensors.cpp
 * @author Daniel Kim
 * @brief Reads sensor from our 9dof sensor array
 * @version 0.1
 * @date 2022-06-28
 *
 * @copyright Copyright (c) 2022 OceanAI (https://github.com/daniel360kim/OceanAI)
 *
 */

#include "Sensors.h"
#include "../Data/StartInfo.h"
#include "../core/debug.h"
#include "../core/pins.h"

namespace Sensors
{
    static Angles_3D<double> gyro_bias;
    static volatile bool bar_flag;
    static volatile bool accel_flag;
    static volatile bool gyro_flag;
    static volatile bool mag_flag;
 
    static Bmi088Accel accel;
    static Bmi088Gyro gyro;
 
    static LIS3MDL mag;

    static BMP388_DEV baro;

    static int64_t previous_mag_time = 0;

    /*
    BMI088 comes with built in low pass filter
    LIS3MDL does not come with built in low pass filter so we use our own
    */
    Filter::LowPass<1> mag_x;
    Filter::LowPass<1> mag_y;
    Filter::LowPass<1> mag_z;

    /**
     * @brief Initializes the accelerometer on the BMI088
     *
     * @return true accelerometer initialized successfully
     * @return false accelerometer failed to initialize
     */
    bool initAccel()
    {
        int status = accel.begin();
        accel.pinModeInt1(Bmi088Accel::PUSH_PULL, Bmi088Accel::ACTIVE_HIGH);
        accel.mapDrdyInt1(true);
        accel.setRange(Bmi088Accel::RANGE_3G);

        // Saving the configurations to the StartInfo struct
        configs.accel_range = (char *)"Accel: 3G";
        configs.accel_ODR = (char *)"Accel ODR: 800Hz";

        if (status < 0)
        {
            ERROR_LOGf(Severity::ERROR, "Accel: Failed to initialize. Error code: %d", status);
            return false;
        }
        else
        {
            SUCCESS_LOG("Accel: Initialized");
            return true;
        }
    }

    /**
     * @brief Initializes the gyroscope on the BMI088
     *
     * @return true gyroscope initialized successfully
     * @return false gyroscope failed to initialize
     */
    bool initGyro()
    {
        int status = gyro.begin();
        gyro.setOdr(Bmi088Gyro::ODR_1000HZ_BW_116HZ);
        gyro.pinModeInt3(Bmi088Gyro::PUSH_PULL, Bmi088Gyro::ACTIVE_HIGH);
        gyro.mapDrdyInt3(true);
        gyro.setRange(Bmi088Gyro::RANGE_250DPS);

        // Saving the configurations to the StartInfo struct
        configs.gyro_range = (char *)"Gyro: 2000dps";
        configs.gyro_ODR = (char *)"Gyro ODR: 3200Hz";

        if (status < 0)
        {
            ERROR_LOGf(Severity::ERROR, "Gyro: Failed to initialize. Error code: %d", status);
            return false;
        }
        else
        {
            SUCCESS_LOG("Gyro: Initialized");
            return true;
        }
    }

    /**
     * @brief Initializes the magnetometer on the LIS3MDL
     *
     * @return true magnetometer initialized successfully
     * @return false magnetometer failed to initialize
     */
    bool initMag()
    {
        if (!mag.init())
        {
            ERROR_LOG(Severity::ERROR, "Mag: Failed to initialize");
            return false;
        }
        else
        {
            SUCCESS_LOG("Mag: Initialized");
        }

        mag.enableDefault();

        // Saving the configurations to the StartInfo struct
        configs.mag_range = (char *)"Mag: +/- 4 Gauss";
        configs.mag_ODR = (char *)"Mag ODR: 1000Hz";
        configs.mag_bias = {mag_bias.x, mag_bias.y, mag_bias.z};

        // Setting the cutoff frequency for the mag low pass filter
        mag_x.setCutoff(30);
        mag_y.setCutoff(30);
        mag_z.setCutoff(30);

        return true;
    }

    /**
     * @brief Initializes the barometer on the BMP388
     *
     * @return true barometer initialized successfully
     * @return false barometer failed to initialize
     */
    bool initBaro()
    {
        if (!baro.begin(BMP388_I2C_ALT_ADDR))
        {
            ERROR_LOG(Severity::ERROR, "Baro: Failed to initialize");
            return false;
        }
        else
        {
            SUCCESS_LOG("Baro: Initialized");
        }

        baro.setPresOversampling(OVERSAMPLING_X4);
        baro.setTempOversampling(OVERSAMPLING_X16);
        baro.enableInterrupt();
        baro.setTimeStandby(TIME_STANDBY_80MS);
        baro.startNormalConversion();

        // Saving the configurations to the StartInfo struct
        configs.BMP_os_p = (char *)"Pressure: X4";
        configs.BMP_os_t = (char *)"Temperature: X16";
        configs.BMP_ODR = (char *)"Standby: 80 milliseconds";
        
        return true;
    }

    /**
     * @brief Initializes all the sensors on the sensor array
     * 
     * @return true all sensors initialized successfully
     * @return false a sensor failed to initialize
     */
    bool initAll()
    { 
        //Individual functions handle logging to debugger
        if (!initAccel())
        {
            return false;
        }
        if (!initGyro())
        {
            return false;
        }
        if (!initMag())
        {
            return false;
        }
        if (!initBaro())
        {
            return false;
        }

        return true;
    }

    /**
     * @brief Scans all the I2C addresses and returns the addresses of the devices found
     *
     * @return std::vector<uint8_t> vector of addresses of the devices found
     */
    std::vector<uint8_t> scanI2C()
    {
        uint8_t error = 0;
        uint8_t address = 0;
        int nDevices = 0;

        for (address = 1; address < 127; address++)
        {
            Wire.beginTransmission(address);
            error = Wire.endTransmission();

            if (error == 0)
            {
                INFO_LOGf("I2C device found at address 0x%d", address);
                configs.addresses.push_back(address); // Saving the address to the StartInfo struct
                nDevices++;
            }
            else if (error == 4)
            {
                INFO_LOGf("Unknow error at address 0x%d", address)
            }
        }

        configs.num_devices = nDevices; // How many devices were found
        return configs.addresses;       // Returning the addresses of the devices found
    }

    /**
     * @brief Configures interrupt ISRS from specific sensors
     *
     * @param bar_int pin that the barometer interrupt is connected to
     * @param accel_int pin that the accelerometer interrupt is connected to
     * @param gyro_int pin that the gyroscope interrupt is connected to
     * @param mag_int pin that the magnetometer interrupt is connected to
     */
    void setInterrupts(const uint8_t bar_int, const uint8_t accel_int, const uint8_t gyro_int, const uint8_t mag_int)
    {
        // Setting the interrupt pins as inputs
        pinMode(bar_int, INPUT);
        pinMode(accel_int, INPUT);
        pinMode(gyro_int, INPUT);
        pinMode(mag_int, INPUT);
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

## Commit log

2022-07-13 init commit
    [Back_flange.step, IMU.kicad_sch, M3 X 10mm Screw v3.f3d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]
2022-07-14 Optimized OV2640 camera operation
2022-07-23 start information logging
    [LP5900SD-3.3_NOPB.step, atsamd21.kicad_sch, bmp388.kicad_sch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]
2022-07-25 created stepper motor driver
2022-07-27 finished board schematic
    [LTC3411.kicad_sch, LTC4311IDCPBF.step, atsamd21.kicad_sch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]
2022-07-27 reordered directories
    [IMU.kicad_sch, LP5900SD-3.3_NOPB.step, LTC3411.kicad_sch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]
2022-07-27 created PCB readme
2022-07-27 updated schematics
    [1054550101.step, BMP388.STEP, BQ24074RGTRG4.STEP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]
2022-07-28 completed PCB layout
    [atsamd21.kicad_sch, transmitter.kicad_pcb, transmitter.kicad_sch]
2022-07-28 created fabrication outputs
    [transmitter-B_Cu.gbr, transmitter-B_Mask.gbr, transmitter-B_Paste.gbr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]
2022-07-29 created sensor board
    [atsamd21.kicad_sch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]
2022-08-12 created sensor_board configs
2022-08-12 i2c send data impl
2022-08-13 external sensor support
2022-08-14 communication with sensor board
2022-08-20 completed stepper driver
2022-09-11 switched to static queue instead of dynamic
2022-09-11 changed sensor class to singleton
2022-09-13 stepper utility
2022-09-13 added barometer filtering
2022-09-24 switched to std::queue instead of CircularBuffer
2022-09-24 updated buoyancy stepper
2022-09-24 fixed LED pin defs
    [pins.h]
2022-10-01 updated to nanosecond resolution timers
2022-10-01 fixed ns to sec conversion factors
    [SD.cpp, main.cpp]
2022-10-02 created timer class
2022-10-02 switched to dynamic queue
2022-10-29 removed sensor driver
2022-11-06 updated external sensor API
2022-11-23 updated camera API
2022-11-25 updated json parse
    [data00.csv, data02.csv]
2022-11-26 removed pitch data transmission
2022-12-04 updated stepper functionality
2022-12-29 created gitignore for PCB
2022-12-29 updated schematic 3d models
    [main_board.kicad_pcb, main_board.kicad_sch, pow.kicad_sch]
2022-12-29 made logged data more specific
    [configuration.h]
2022-12-29 changed from singleton -> individual functions
    [configuration.h]
2023-01-01 updated CAD model
    [Back_flange.step, M3 X 10mm Screw v3.f3d, M3 X 10mm Screw.SLDPRT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]
2023-01-01 added GUI configurations
    [configuration.h]
2023-01-01 changed transport monitor interval to 5Hz
    [configuration.h]
2023-01-01 added UI and Debug output collision warning
    [configuration.h]
2023-01-02 removed mission duration object
    [configuration.h]
2023-01-03 removed unneeded includes
    [configuration.h]
2023-01-03 removed disfunctional back to top button
2023-01-20 updated 3D board models
2023-01-20 added new images
    [configuration.h]
2023-01-21 created data extractor
    [long.csv]
2023-02-04 updated nomenclature of schematic
2023-02-15 updated schematic labels
    [IMU.kicad_sch, TDS.kicad_sch, barometer.kicad_sch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]
2023-02-15 removed unneeded data files
    [data00.csv, data02.csv]
2023-02-15 updated json parser example data
    [data112.csv]
2023-02-15 removed error manager class
    [debug.cpp]
2023-02-15 updated hitl functionality on auv
    [configuration.h]
2023-02-25 updated main board layers
2023-03-10 added numeric outputs to navigation page
    [configuration.h]
2023-03-10 updated camera features
2023-04-03 allow for multiple voltage readings
2023-04-03 fixed pin nomenclature
2023-04-03 removed unneeded diving state
    [configuration.h]
2023-04-03 fixed led test code
    [main.cpp]
2023-04-04 more documentation and cleanup
    [configuration.h]
2023-04-05 added automatic pitch control
2023-04-05 made stepper controls more concise
    [configuration.h]
2023-04-06 added pitch control mechanism
2023-04-06 added pitch control within the pitch class
    [configuration.h]
2023-04-23 changed positions for automated pitch control

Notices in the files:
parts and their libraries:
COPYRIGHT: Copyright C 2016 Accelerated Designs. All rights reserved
